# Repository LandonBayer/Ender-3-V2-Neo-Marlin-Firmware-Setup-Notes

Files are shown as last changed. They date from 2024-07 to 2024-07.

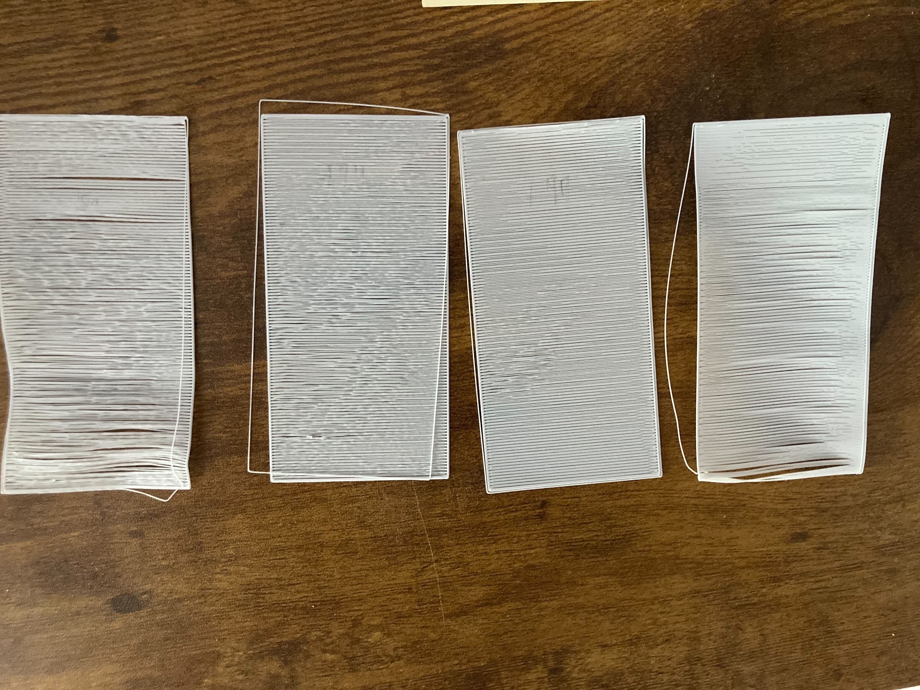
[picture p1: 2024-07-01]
probeoffsetcalibrationlayers.jpg

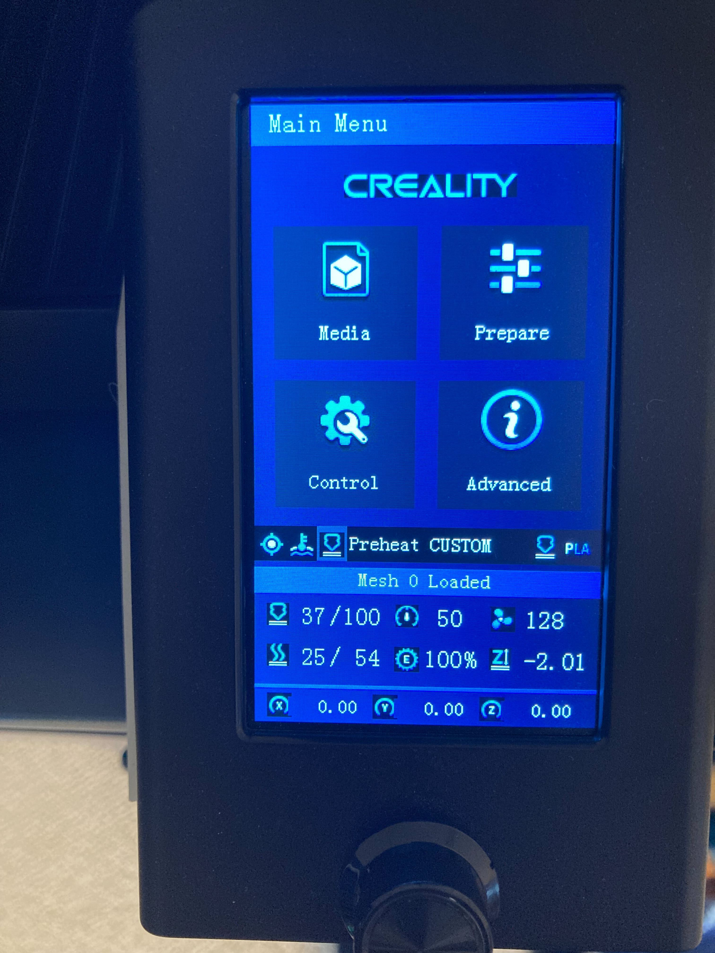
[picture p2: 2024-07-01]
printerscreen.jpg

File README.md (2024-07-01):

# Ender-3-V2-Neo-Marlin-Firmware-Setup-Notes

Hi everyone! 

I'm going to go through some of my notes, struggles, etc while setting up my V2 Neo this year. I'd like to preface by saying that this is **NOT** the best printer to buy nowadays, as many better options are available even at a similar price. 

To begin, I ran into an issue almost instantly after starting my printer. I checked and **made sure to be on 120V beforehand using the switch on the back**, then turned it on. Everything seemed fine at first, but when I started a print, nothing happened at all. The preview showed 0 time, 0 layers, 0% complete, and so forth. With the default firmware, it wouldn't even print.

Luckily, I had planned to upgrade my printer firmware before even getting the printer. Using this guide: https://lash-l.github.io/ender3_v2_neo/firmware_update , I was able to do so with some struggles. I began by attempting to do this as instructed, building my own version of Marlin (the firmware) and compiling it to the microSD card for the printer. I did everything as best I could, but it would not compile onto the card for me. I am not particularly skilled with this sort of development, so it's likely my own error, but nonetheless I had to find another way.

Instead, I used a different guide that was for a different printer (Ender 3 V2) but it worked for mine as well. Here is the link: https://github.com/mriscoc/Ender3V2S1/wiki/How-to-install-the-firmware . After downloading the appropriate binary, I put it on my SD card and into the printer. This time, it seemed to turn on properly, but the screen was still off. Going back to the old guide, I opened it up and found out that it was a TJC screen, naturally the only one that needs to have firmware flashed, I downloaded it and used the same SD card to install it, then went back to the main machine where FINALLY it booted up properly. Although this doens't sound like much, all of this took about 2 hours total. 

Now that it was finally functioning, I continued with the first guide section called "Fine Tuning", which led me through setting up my slicer properly with good presets for different speeds and qualities, leveling the bed, getting the Z offset, etc. These all took about an hour total, and after I was able to start printing! However, there were still significant issues that bothered me, there were strange sections in prints that resembled elephants foot partway through but consistent across prints, seams, some small gaps on the first layer, and more. Let's go into detail on those.

### Slicer
Using the profiles in that guide, I had few issues getting my slicer configured and working for my printer. Cura is quite user friendly, so I had no trouble there.

### Leveling the bed
Now this is where I got stuck for a while. I used the bed tramming feature in Marlin, which probes each corner to tell you the offset and you adjust them to fix it. I adjusted all of mine to just about 0, which seemed great to me. I re-homed the printer, just to be sure, and suddenly they were all around .2mm again. I put them back to 0, did it again, and they were back to .2mm. I realized after a bit that instead of targeting 0, I had to **target about .20mm** for it to be consistent across prints. After, I had few issues with the tramming and didn't notice many issues in the prints due to it.

### Getting my Z offset
Just about everything online recommends using paper, which I did, and setting the probe off that test. This setting seemed to work fine and I didn't change it until today, where I began experimenting further. Using this model: https://www.printables.com/model/78307-z-offset-calibration-print , I was able to check for how to adjust my Z offset (Note: I already tuned my e-steps for the extruder, so over-under extrusion shouldn't be a factor. You can learn about this in the lash-l guide linked above). In doing so, I ended up realizing that it was about .1mm too high, and adjusting that helped with accuracy in my prints. Check out the image **probeoffsetcalibrationlayers.png** above to see it. It shows four single layer infill tests I printed to find my optimal Z probe offset. From left to right, the numbers are (in millimeters): -1.89,-1.94,-1.99,-2.04. Out of the options, the best looking one to me was -1.99, but a bit extra seems to help so I set mine at -2.01 going forward.

To elaborate, you can clearly see the gaps in my original setting of 1.89, and they remain in 1.94 to a lesser degree. At 1.99 they become smaller and more uniform, and at 2.04 the entire piece was stuck to the bed and bent when removed, showing some possible squish even with the gaps. For now, I'm sticking with that sweet spot of 2.01 that should work well.

### Print quality
In many of my prints, there was a significant band about 3/4" above the surface plate on every print. I tried flipping the lead screw, but the issue remained. After some research, I adjusted the tension on both the lead screw nut and the eccentric nuts on the Z axis. For the lead screw, **I tightened both bolts hand tight with the allen wrench, then released each by half a turn.** This added some slack that assisted with the binding in spots. I also **loosened and then lightly snugged up the nuts by the V wheels on each side**, to provide some tension but not so much as to resist the movement of the axis. These changes seemed to greatly decrease the band, making for much nicer prints. It also, alongside the Z offset change, made it possible to print at a .2mm layer height, instead of only .28mm before (it wouldn't stick to the bed at all, which in hindsight makes a lot of sense). You can see this huge difference in the image **bandingcomparison.jpg** above: left is before fixing Z axis binding (you can see the very obvious band) right is after these adjustments were made.

### Mesh leveling
As far as I can tell, it does it's job. One thing to note is to be sure to **preheat the bed, then home, then level.** I personally added a custom preheat setting to the toolbar on the main screen of the printer that heats the bed to 55°C and the nozzle to 100°C to make the startup for printing faster. If you only press the mesh level without pre-heating, it will home before heating the bed, throwing your entire mesh completely off. 

### Useful tips
If you use Cura, there is also a plug-in you can add to give you a picture preview of the part on the screen of the printer, which I have installed. Learn more here: https://github.com/mriscoc/Ender3V2S1/wiki/How-to-generate-a-gcode-preview 

### Personal Preference

I also printed a couple things to make my printer work a bit better. First, I found a screenholder that moves it closer in front and within the footprint of the printer (I can't find the source anymore, but hopefully mine is better anyways). However, it uses additional hardware to mount, which I didn't have. I adjusted the model to have slots built in that slide into the aluminum extrusion of the printer. You can find my model here or uploaded to this repo: https://cad.onshape.com/documents/af33bdea7fdd3ea30d09401f/w/1ec14669289cab5e2b495bab/e/6b54fc4dcec8c699b5a798f2 . Secondly, I printed a side spool holder to reduce strain on the filament when printing (https://www.thingiverse.com/thing:4748139). I also attempted to create a 3D printed bearing for the filament roller, as I noticed it getting stuck constantly when feeding. My printer probably wasn't tuned well enough to make it work, so it had too much friction and didn't actually spin. Luckily, the PLA on the surface of the spool holder itself had much less friction, making for a smoother turning action. My recommendation is to just print a thin cylinder to hold it up and give it a bit less friction.

Also, I customized my toolbar to have the things I find most useful. You can see what it looks like in the image **printerscreen.jpg** above. My config is auto home, cooldown, preheat Custom (100 nozzle, 54 bed), Auto build mesh, and preheat PLA (180 nozzle, 60 bed).

### I hope this helped, thanks for reading!

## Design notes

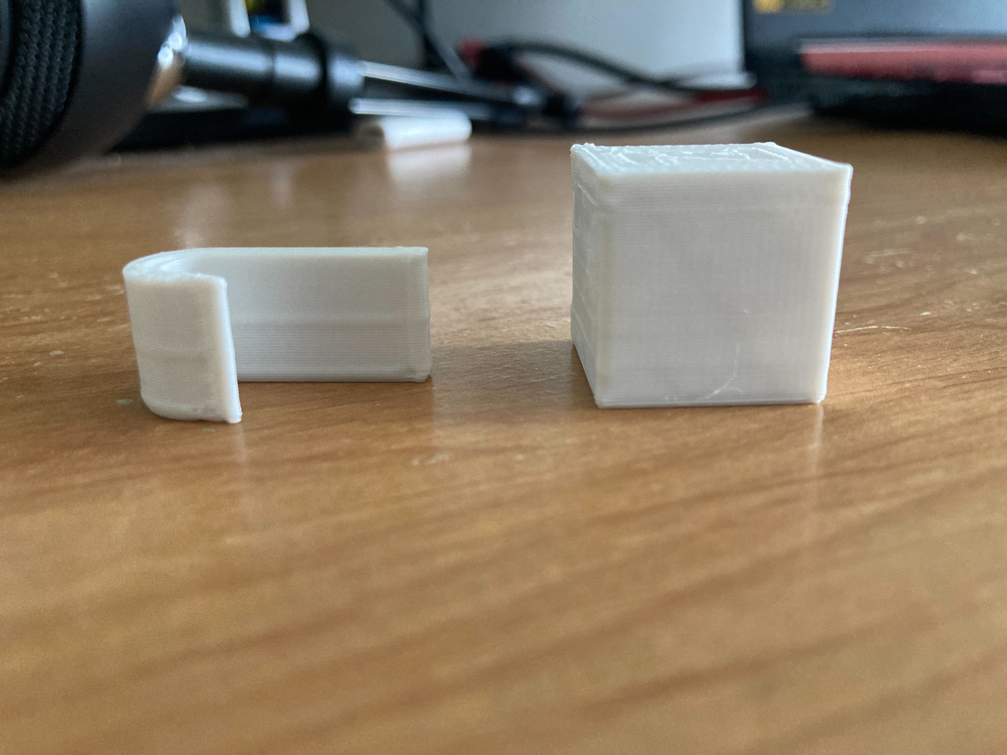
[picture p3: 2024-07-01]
bandingcomparison.jpg

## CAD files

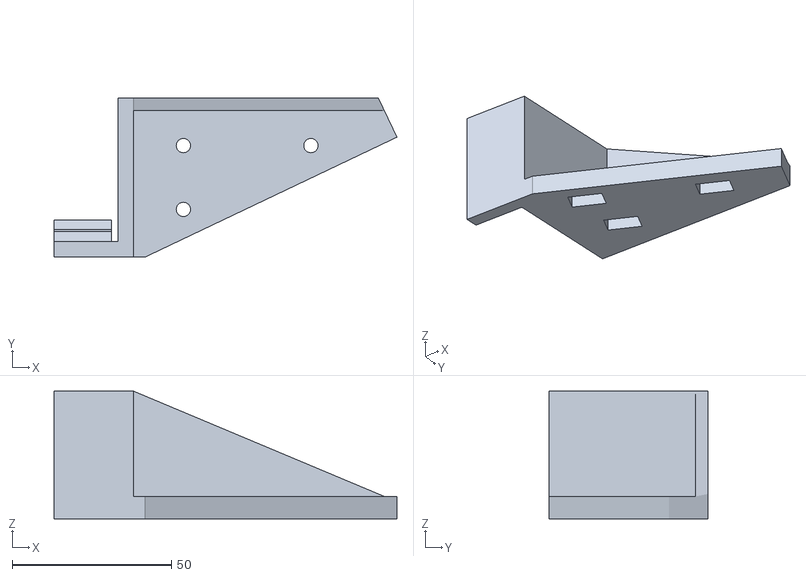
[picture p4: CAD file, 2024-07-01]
ender-3-v2-neo-slim-front-display-mount.stl
107.6 x 50.0 x 40.0
